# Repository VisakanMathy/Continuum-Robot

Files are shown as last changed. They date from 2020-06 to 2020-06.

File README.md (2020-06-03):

# Continuum Robot

The purpose of this repository is to create an open source continuum robot and control system that is accesible using low cost components and 3D printers. It includes a list of SolidWorks part files and a basic arduino library with examples for controls.

## Using the CAD
Begin by downloading and extracting the [part files and assemblies](ContinuumRobotDesign) to a desired location and then open up the file. You can now edit the [equationsAll.txt](ContinuumRobotDesign/equationsAll.txt) file and explore changing parameters. Some key parameters are indicated in the following table:

Parameter | Orginal Value
------------ | -------------
Spine Diameter | 15 mm
Disc Thickness | 4mm
Ligament Angle | 40&deg;
Ligament Width | 2mm
Disc Seperation | 6mm
No. Disc/Segment | 5
No. Segments | 3

Once you are configured, you can print and assemble your continuum robot.

## Setting up
Make sure to attach the header pins to the channels in the coorect order with channel 0-3 being dedicated to the segment closest to the base and attached with zero at the top and follows round clockwise. Having done so begin exploring the different control methods using the [Core.ino](Continuum/Examples/Core/Core.ino) to get started and once you're setup you can test your robot using [WorkspaceExploration.ino](Continuum/Examples/WorkspaceExploration/WorkspaceExploration.ino)

## The Arduino Library
Begin by installing the Continuum library and the [Adafruit_PWMServoDriver](https://github.com/adafruit/Adafruit-PWM-Servo-Driver-Library) library. Once installed it is recommended to set up a single servo motor by utilising the examples and tutorials available on [Adafruit](https://learn.adafruit.com/16-channel-pwm-servo-driver/). It is important recollect the boundary frequency values to transition into this library.

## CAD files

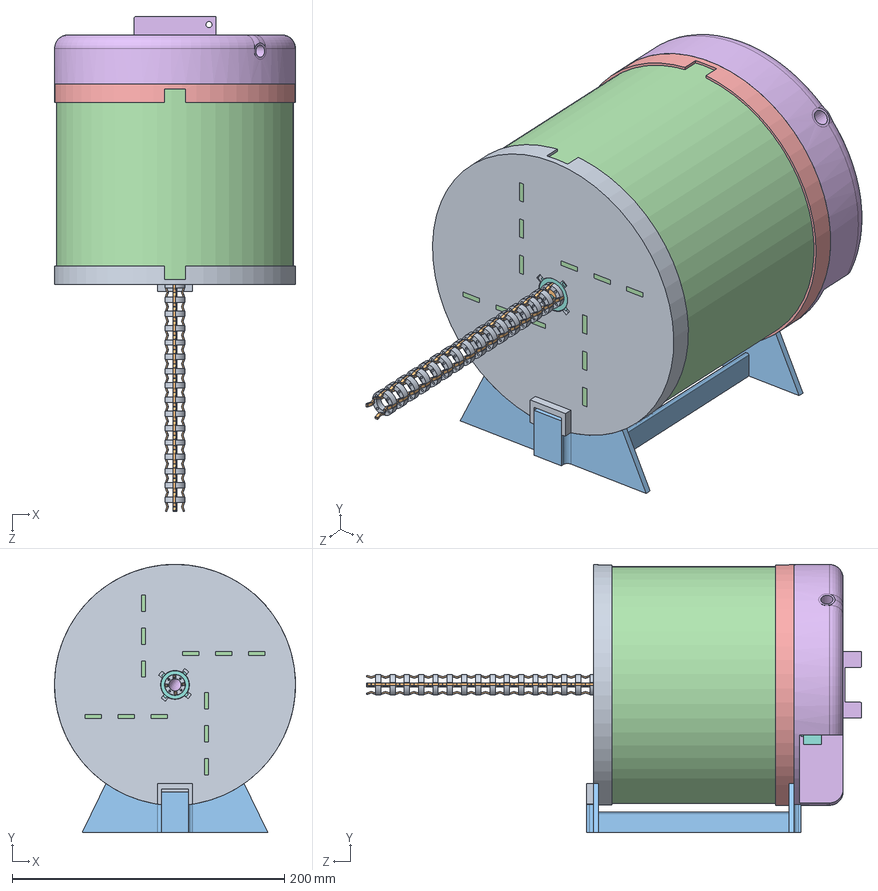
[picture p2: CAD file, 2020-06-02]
Continuum Robot Design/ContinuumRobot.SLDASM
177.2 x 197.2 x 363.9 mm
FrontCover
55gServoMotor x 12
CircularAttachment x 12
ServoHolderDirect x 4
MotorTransmissionMedium x 4
MotorTransmissionSmall x 4
MotorTransmissionLarge x 4
SpineTwistLock
RigidDisc x 16
Ligament x 4
BaseHolder
HubCover
BackCover
URVMount
ServoDriver
arduinoUnor

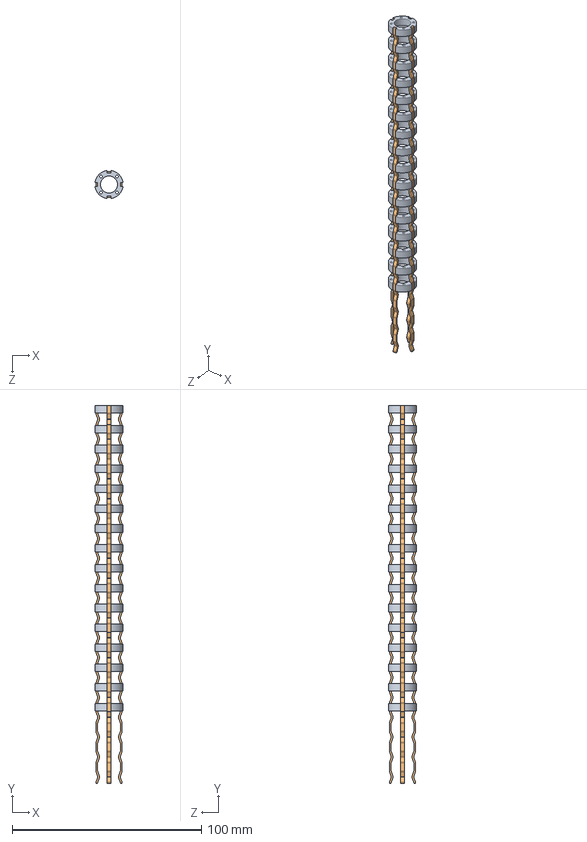
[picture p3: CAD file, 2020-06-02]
Continuum Robot Design/Spine/Spine3Segments.SLDASM
14.8 x 199.8 x 14.8 mm
RigidDisc x 16
Ligament x 4

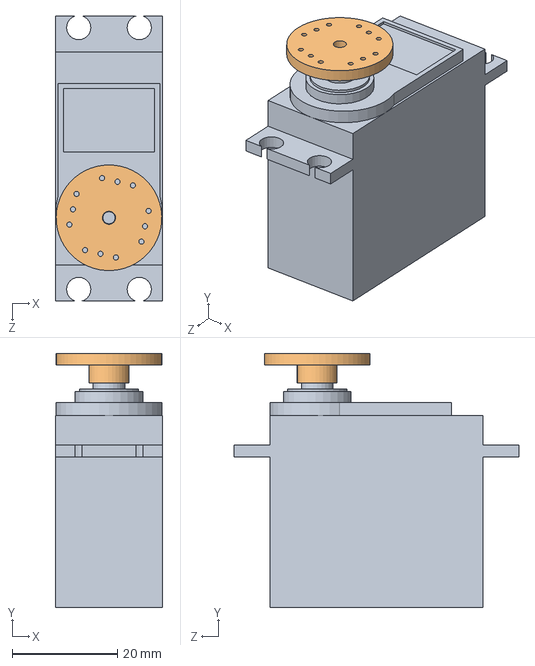
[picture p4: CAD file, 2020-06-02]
Continuum Robot Design/Electronics/55gServoAndAttachment.SLDASM
20.3 x 48.3 x 54.1 mm
55gServoMotor
CircularAttachment

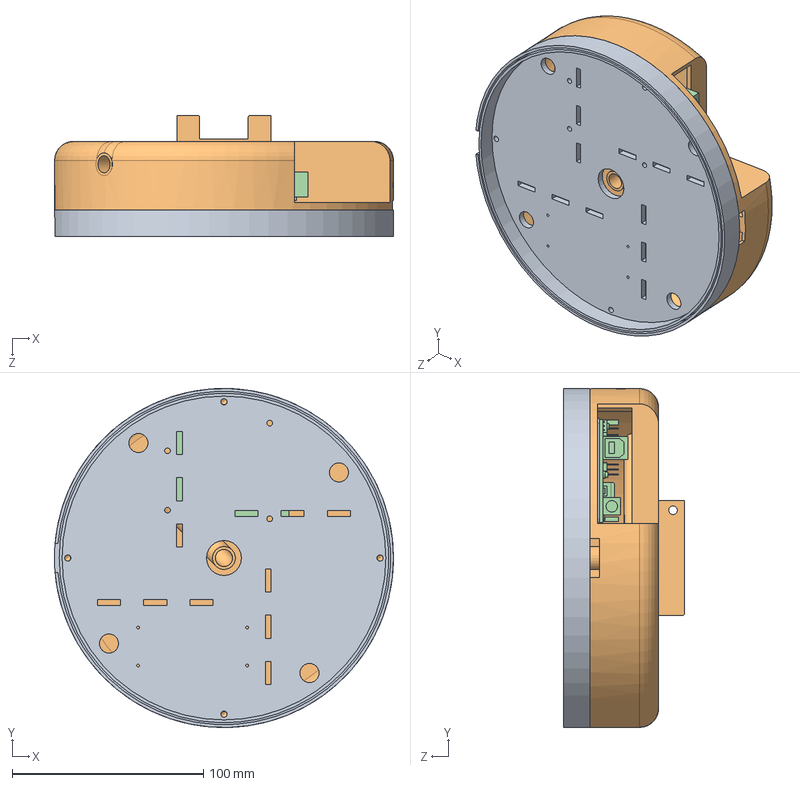
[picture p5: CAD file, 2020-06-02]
Continuum Robot Design/ControlMechanism/MountAndBack.SLDASM
177.2 x 177.2 x 63.2 mm
BackCover
URVMount
ServoDriver
arduinoUnor

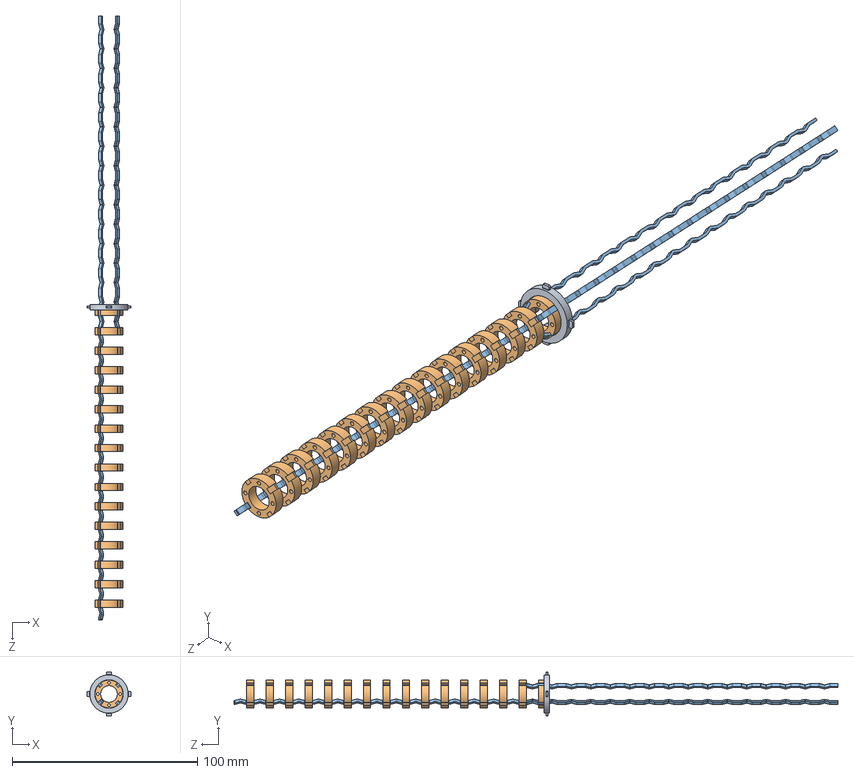
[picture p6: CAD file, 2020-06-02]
Continuum Robot Design/Spine/SpineAndLock.SLDASM
23.7 x 23.7 x 325.8 mm
SpineTwistLock
RigidDisc x 16
Ligament x 4

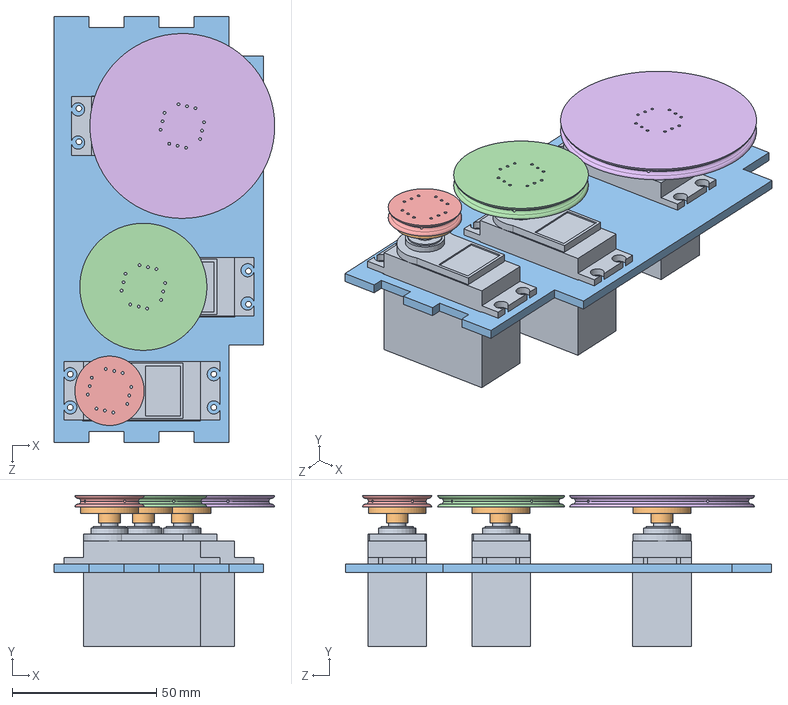
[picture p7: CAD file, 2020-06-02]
Continuum Robot Design/ControlMechanism/ServoSet.SLDASM
76.3 x 52.3 x 147.5 mm
55gServoMotor x 3
CircularAttachment x 3
ServoHolderDirect
MotorTransmissionMedium
MotorTransmissionSmall
MotorTransmissionLarge

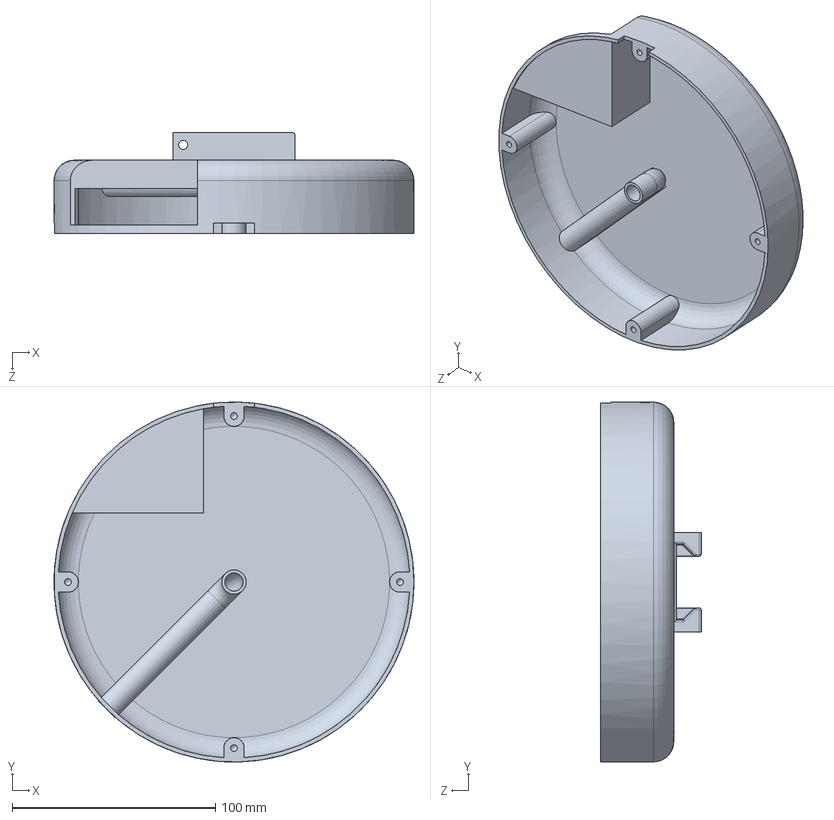
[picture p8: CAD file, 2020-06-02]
Continuum Robot Design/ControlMechanism/URVMount.SLDPRT
177.2 x 177.2 x 49.5 mm

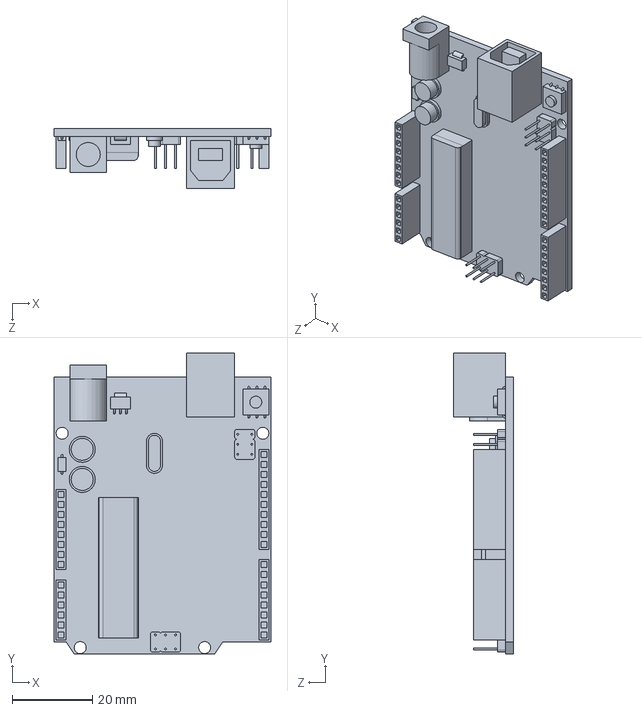
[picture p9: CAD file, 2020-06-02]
Continuum Robot Design/Electronics/arduinoUnor.SLDPRT
54.0 x 75.0 x 15.0 mm

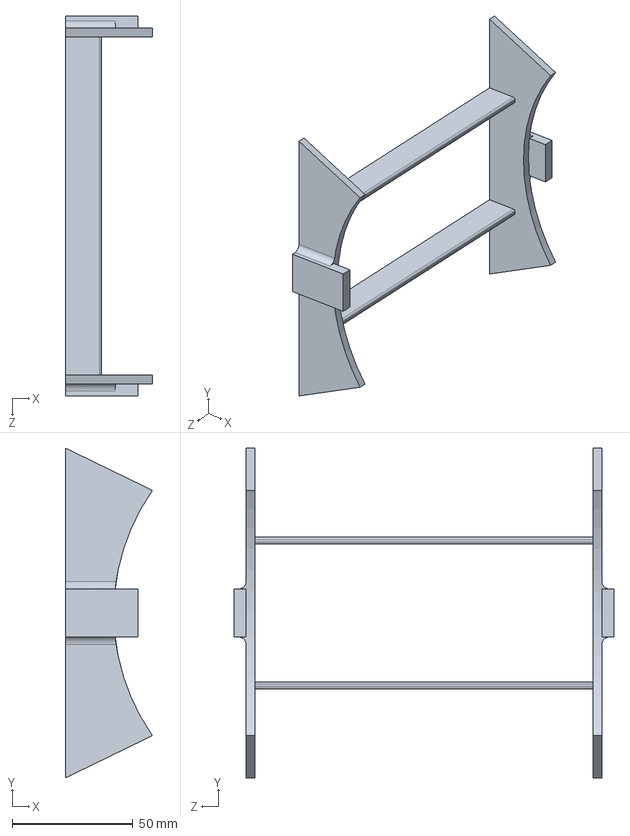
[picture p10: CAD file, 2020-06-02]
Continuum Robot Design/Supports/BaseHolder.SLDPRT
36.0 x 136.7 x 157.5 mm

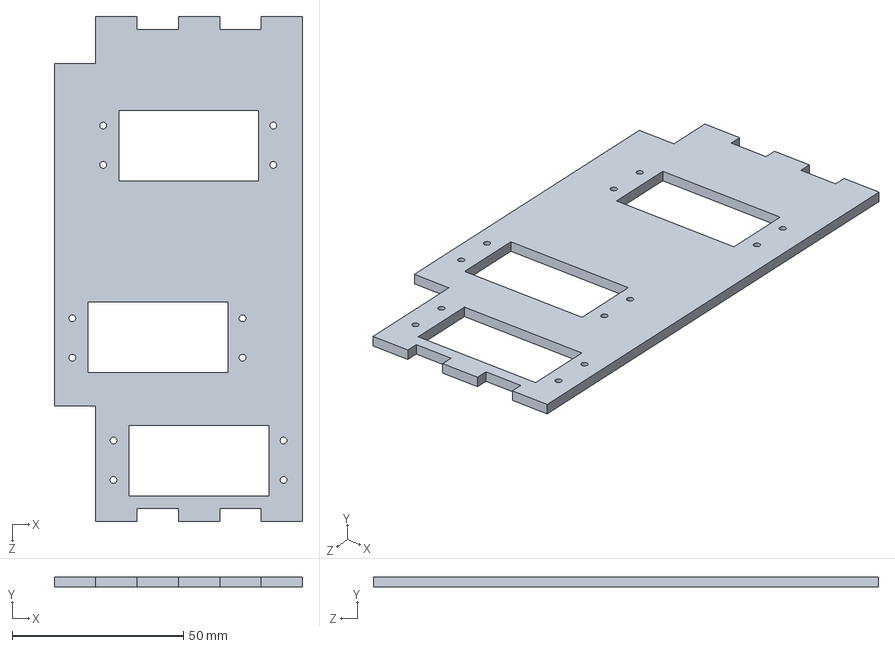
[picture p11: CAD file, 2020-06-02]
Continuum Robot Design/ControlMechanism/ServoHolderDirect.SLDPRT
72.5 x 3.00 x 147.5 mm

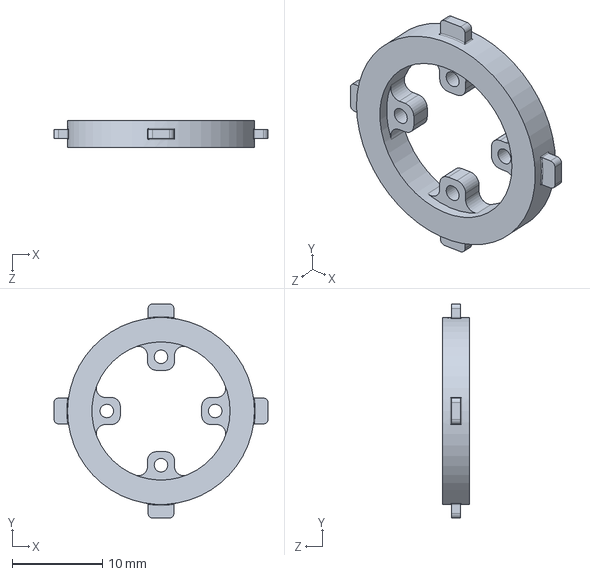
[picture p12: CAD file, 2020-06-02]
Continuum Robot Design/Spine/SpineTwistLock.SLDPRT
23.7 x 23.7 x 3.00 mm

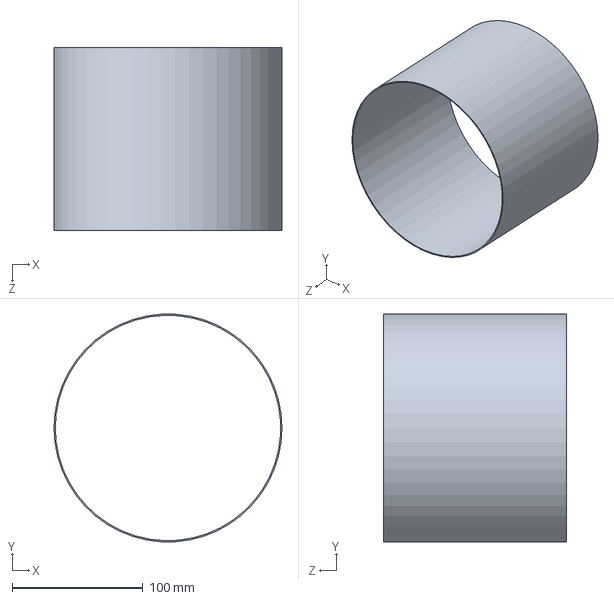
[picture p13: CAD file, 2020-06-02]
Continuum Robot Design/Supports/HubCover.SLDPRT
174.2 x 173.9 x 140.0 mm

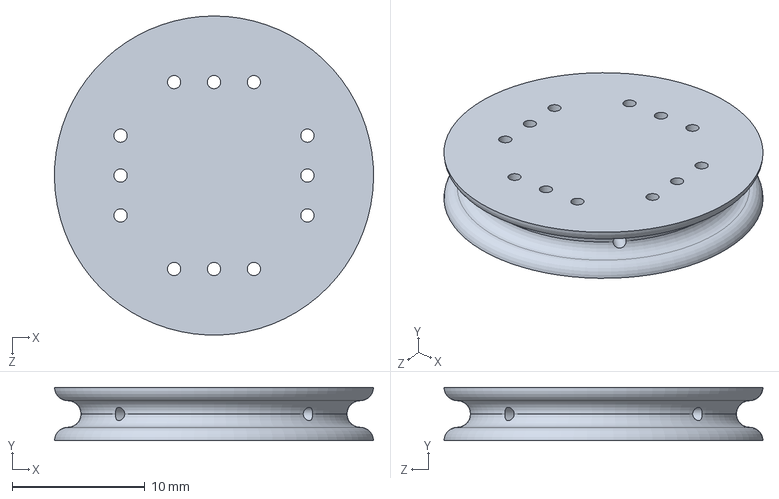
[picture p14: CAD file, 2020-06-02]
Continuum Robot Design/ControlMechanism/MotorTransmissionSmall.SLDPRT
24.0 x 4.00 x 24.0 mm

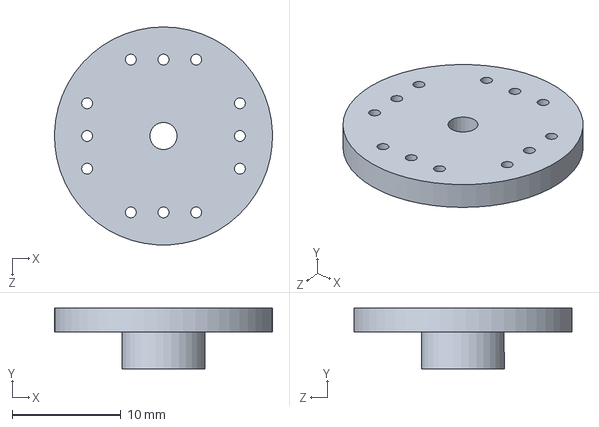
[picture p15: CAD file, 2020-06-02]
Continuum Robot Design/Electronics/CircularAttachment.SLDPRT
20.0 x 5.60 x 20.1 mm

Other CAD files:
Continuum Robot Design/Spine/Ligament.SLDPRT
Continuum Robot Design/Electronics/55gServoMotor.SLDPRT
Continuum Robot Design/ControlMechanism/MotorTransmissionMedium.SLDPRT
Continuum Robot Design/Electronics/ServoDriver.SLDPRT
Continuum Robot Design/ControlMechanism/BackCover.SLDPRT
Continuum Robot Design/ControlMechanism/FrontCover.SLDPRT
Continuum Robot Design/ControlMechanism/MotorTransmissionLarge.SLDPRT
Continuum Robot Design/Spine/RigidDisc.SLDPRT

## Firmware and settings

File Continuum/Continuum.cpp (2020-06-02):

#include "Arduino.h"
#include "Wire.h"
#include "Adafruit_PWMServoDriver.h"
#include "Continuum.h"

Continuum::Continuum(int startAngle)
{
    for (int i = 0; i < 12; i++)
    {
        _angleArray[i] = startAngle;
    }
    pwm = Adafruit_PWMServoDriver();
}
Continuum::Continuum(int startAngle, int sections)
{
    _sections = sections;
    for (int i = 0; i < sections * 4; i++)
    {
        _angleArray[i] = startAngle;
    }
    pwm = Adafruit_PWMServoDriver();
}
void Continuum::pwmSetup()
{
    pwm.begin();
    pwm.setOscillatorFrequency(27000000);
    pwm.setPWMFreq(_SERVO_FREQ);
}
void Continuum::setPWMBounds(int SERVOMIN, int SERVOMAX)
{
    _SERVOMIN = SERVOMIN;
    _SERVOMAX = SERVOMAX;
}
void Continuum::setCardinalTuner(double cardTuner)
{
    _cardTuner = cardTuner;
    Serial.print("Directional Tuning: ");
    Serial.println(_cardTuner);
}
void Continuum::setSectionTuner(double sectionTuner)
{
    _sectionTuner = sectionTuner;
    Serial.print("Sectional Tuning: ");
    Serial.println(_sectionTuner);
}
double Continuum::pulseLength(double angle) { return constrain(map(angle, 0, 180, _SERVOMIN, _SERVOMAX), _SERVOMIN, _SERVOMAX); }
void Continuum::startPull()
{
    Serial.println("{");
    for (int i = 0; i < _sections * 4; i++)
    {
        Serial.print(_angleArray[i]);
        Serial.print("\t");
        pwm.setPWM(i, 0, pulseLength(_angleArray[i]));
    }
    Serial.println("}");
}
void Continuum::pullIncrement(int section, double incrementAngle, int card)
{
    for (int i = 0; i < section - 1; i++)
    {
        _angleArray[4 * i + card] += incrementAngle;
        _angleArray[4 * i + ((card + 3) % 4)] += _cardTuner * (incrementAngle * _sectionTuner);
        _angleArray[4 * i + ((card + 1) % 4)] += _cardTuner * (incrementAngle * _sectionTuner);
    }
    for (int i = section - 1; i < _sections; i++)
    {
        _angleArray[4 * i + card] += (incrementAngle * section) / (i + 1);
        _angleArray[4 * i + ((card + 3) % 4)] += _cardTuner * ((incrementAngle * section) / (i + 1));
        _angleArray[4 * i + ((card + 1) % 4)] += _cardTuner * ((incrementAngle * section) / (i + 1));
    }
}
void Continuum::setAngles(double angleArray[])
{
    for (int i = 0; i < _sections * 4; i++)
    {
        _angleArray[i] = angleArray[i];
    }
    startPull();
}
void Continuum::singleServoAdjust(int section, double angle, int card)
{
    _angleArray[4 * (section - 1) + card] = angle;
    startPull();
}
double Continuum::currentAngle(int section, int card)
{
    return _angleArray[4 * (section - 1) + card];
}

void Continuum::easyPull(int section, int incrementAngle, int card)
{
    float angle = ((card % 90) * M_PI) / 180;
    if (card % 90 == 0)
    {
        pullIncrement(section, incrementAngle, card / 90);
    }
    else
    {
        _angleArray[4 * (section - 1) + (card / 90)] += incrementAngle * (tan(angle) + 2 * (180 / incrementAngle) - 2) / 1 + tan(angle);
        _angleArray[4 * (section - 1) + ((card / 90 + 1) % 4)] += incrementAngle * (2 * (180 / incrementAngle) - 1 - (tan(angle) + 2 * (180 / incrementAngle) - 2) / 1 + tan(angle));
    }
    startPull();
}

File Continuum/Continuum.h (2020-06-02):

#ifndef Continuum_h
#define Continuum_h
#include "Arduino.h"
#include "Wire.h"
#include "Adafruit_PWMServoDriver.h"

class Continuum
{
private:
    int _SERVOMIN = 120;  // This is the 'minimum' pulse length count (out of 4096)
    int _SERVOMAX = 500;  // This is the 'maximum' pulse length count (out of 4096)
    int _USMIN = 600;     // This is the rounded 'minimum' microsecond length based on the minimum pulse of 150
    int _USMAX = 2400;    // This is the rounded 'maximum' microsecond length based on the maximum pulse of 600
    int _SERVO_FREQ = 50; // Analog servos run at ~50 Hz updates
    double _angleArray[16];
    int _sections = 3;
    Adafruit_PWMServoDriver pwm;
    double _cardTuner = 0.5;
    double _sectionTuner = 0;

public:
    Continuum(int startAngle);
    Continuum(int startAngle, int sections);
    void pwmSetup();
    void setCardinalTuner(double cardTuner);
    void setSectionTuner(double sectionTuner);
    void setPWMBounds(int SERVOMIN, int SERVOMAX);
    double pulseLength(double angle);
    void startPull();
    void pullIncrement(int section, double incrementAngle, int card);
    void setAngles(double angleArray[]);
    void singleServoAdjust(int section, double angle, int card);
    double currentAngle(int section, int card);
    void easyPull(int section, int incrementAngle, int card);
};
#endif

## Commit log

2020-06-02 CAD designs
    [55gServoAndAttachment.SLDASM, 55gServoMotor.SLDPRT, BackCover.SLDPRT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]
2020-06-02 zip Library for easy arduino install
